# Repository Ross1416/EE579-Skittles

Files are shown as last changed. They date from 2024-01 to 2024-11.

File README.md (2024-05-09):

# EE579-Skittles

## RUSH (Robust Ultrasonic Skittle Hunter)

This repository is for RUSH (Robust Ultrasonic Skittle Hunter). RUSH (shown below) aims to autonomously play a game of skittles in a corridor without user input beyond the start. RUSH is based on a small, simple remote controlled (RC) car that was extensively modified to play the game with the aim of knocking over one or two black skittles while leaving any white skittles untouched. The winner of the game is determined by the quickest car to knock a black skittle over. However, if a white skittle is knocked over at any point in the round by the car, it is disqualified from the round. 

See TDF for more details.

<p align="center">
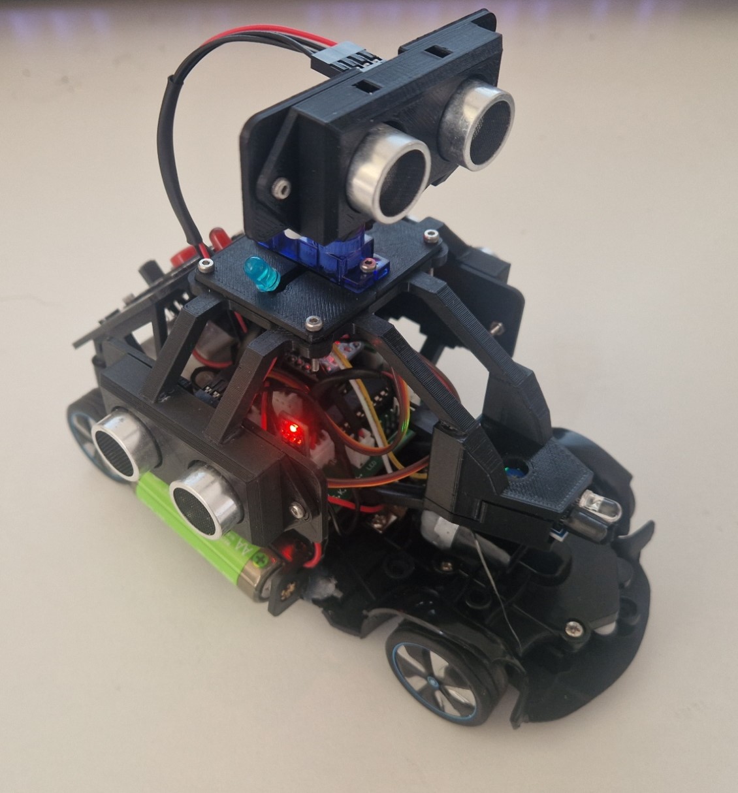
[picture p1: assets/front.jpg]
  
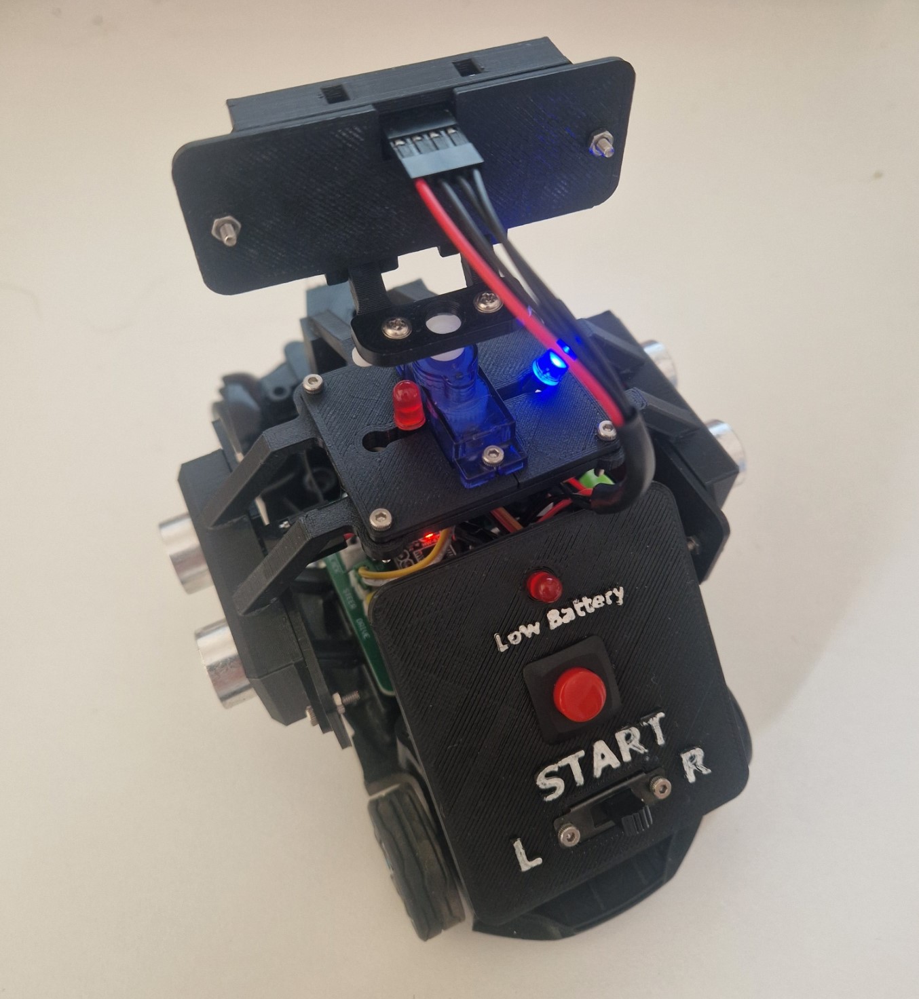
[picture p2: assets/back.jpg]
  
</p>

## Final Demo Day Results

### Heat 1

https://github.com/Ross1416/EE579-Skittles/assets/77679842/c86a0a25-7852-4bd4-9d39-e0872e5b2d3d

### Heat 2

https://github.com/Ross1416/EE579-Skittles/assets/77679842/7563ef13-5aec-49bf-9490-8388c58f7000

### Semi-final

https://github.com/Ross1416/EE579-Skittles/assets/77679842/7b09cfc3-21dd-4e16-b04d-08700aa69c5c

### (Anti-climactic) Final

https://github.com/Ross1416/EE579-Skittles/assets/77679842/db8d8a39-f27a-464d-a305-0642033d31cf

### 2nd Final (for fun)

https://github.com/Ross1416/EE579-Skittles/assets/77679842/e8e8383b-b6d6-447a-95fe-932a4549ee91

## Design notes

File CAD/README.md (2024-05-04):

See videos for disassembly instructions.

Top Sonar Removal

https://github.com/Ross1416/EE579-Skittles/assets/77679842/d813ab6a-119c-48e1-9a04-9669e5136af5

Servo Structure Removal

https://github.com/Ross1416/EE579-Skittles/assets/77679842/874d1653-7c2e-4df4-bafa-91eb13200755

Top Mount Removal

https://github.com/Ross1416/EE579-Skittles/assets/77679842/eb0d6709-a5ab-449e-a856-9e97e344e56b

Control Panel Removal

https://github.com/Ross1416/EE579-Skittles/assets/77679842/7449ef3e-6997-48b8-9b05-bda308c06ea9

Detailed ultrasonic disassbly 

https://github.com/Ross1416/EE579-Skittles/assets/77679842/6136482e-1819-41eb-bea9-b80b4085eafa

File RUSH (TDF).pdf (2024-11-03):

# Robust Ultrasonic Skittle Hunter

# (RUSH)

# Technical Documentation File

Samuel Kliskey | 202028443
Ross Inglis | 202032175
Andrew Law | 202009334
Signature: | Date: 08/05/24
Signature: | Date: 08/05/24

We hereby declare that this work has not been submitted for any other degree/course at this University

or any other institution and that, except where reference is made to the work of other authors, the

material presented is original and entirely the result of our own work at the University of Strathclyde

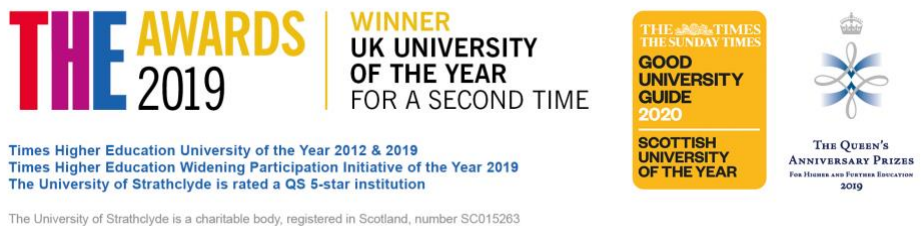
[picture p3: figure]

i

GitHub Repository: https://github.com/Ross1416/EE579-Skittles

## Contents

ii

## Nomenclature

BoM | Bill of Materials
GPIO | General Purpose Input / Output
IC | Integrate Circuit
IR | Infrared
LED | Light Emitting Diode
MSP | Mixed Signal Processor
NiMH | Nickel Metal Hydride
PCB | Printed Circuit Board
PLA | Polylactic Acid
RC | Remote Control
RUSH | Robust Ultrasonic Skittle Hunter
SONAR | Sound Navigation and Ranging
ToF | Time of Flight
uC | Microcontroller

iii

## List of Figures

Figure 12: MSP430G2553 IC (left) [2] , MSP430G2ET Development board (right) [3]

Figure 19: Low Battery Indicator Circuit on Control Board under motor driver (left)

Figure 25: Stages of wiring harness production: strip insulation (left), first stage crimp

Figure 41: Wiring harness (left), Programmer PCB connection (middle) and dev. board

Figure 44: Expected ultrasonic echo waveform at sensor (left) and on control board

iv

Figure 47: Servo test points on control panel | 38
Figure 48: Servo PWM control signal at maximum and minimum angle | 38
Figure 49: Skittle detection with Ultrasonic and Time of Flight (TOF) | 41

## List of Tables

Table 1: HC-SR04 Ultrasonic Sensor Specifications | 6
Table 2: Wiring Harness Connection Specifications | 16
Table 3: MSP430 Functionality and Purpose | 25
Table 4: Ultrasonic Testing expected resistances | 34

## 1 Introduction

This technical specification document details all information regarding RUSH (Robust Ultrasonic

Skittle Hunter) depicted in Figure 1. RUSH aims to autonomously play a game of skittles in a corridor

without user input (after setup) against an opposing car. RUSH is based on a small, simple remote

controlled (RC) car that was retrofitted to play the game and therefore RUSH will commonly be referred

to as the “car” in this document. The aim of the game is to navigate to and knock over one or two black

skittles whilst leaving any white skittles untouched. The winner of the game is determined by the

quickest car to knock a black skittle over. However, if a white skittle is knocked over at any point during

the two minute round by the car, it is disqualified from the round. The skittles were constructed of two

stacked and painted soup cans and are therefore often referred to as “cans” throughout.

This document covers all aspects of RUSH including a quick start user guide and hardware / software

descriptions. Also included is detailed guidance of how to perform troubleshooting and repair should

the car break or behave unexpectedly. This technical specification is intended for anyone with basic

technical knowledge that intends to use the car to play autonomous skittles, understand how it works,

aims to fix any issues that occur or make further improvements.

The base RC car (see Figure 2) that RUSH is based on was to be retrofitted with an array of sensors to

accomplish the goal while adhering to the guidelines stating no alterations to the chassis or drive train.

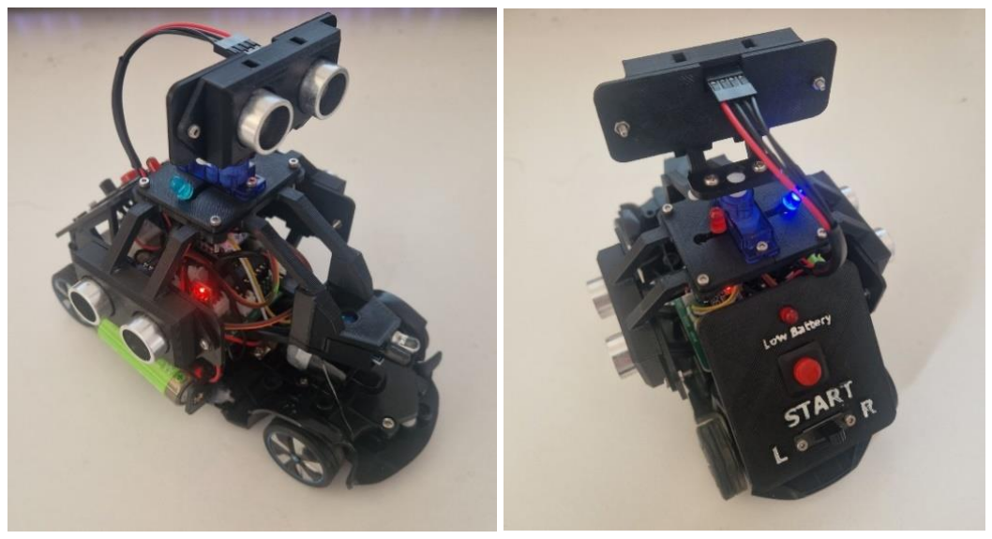
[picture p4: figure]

Figure 1: RUSH viewed from front (left) and rear (right)

Figure 2: Base RC car before modification [1]

## 2 User Guide

This user guide details instructions on how to quickly setup RUSH for a game of skittles. For the car to

function, the game must be setup in a long straight corridor. The corridor should be at least 10 m long

with an expected distance from the start line to the first skittle of at least 6 m. The walls of the corridor

should be unbroken and not have any alcoves or adjoining corridors in the game space as this will

disrupt the cars’ function. Some tolerance of wall geometry changing is accounted for in software but

it performs best where the wall is flat and performs worse if the wall has multiple changes close together

or passes an adjoining corridor. The setup of the car in the corridor should be roughly as seen in

Figure 3.

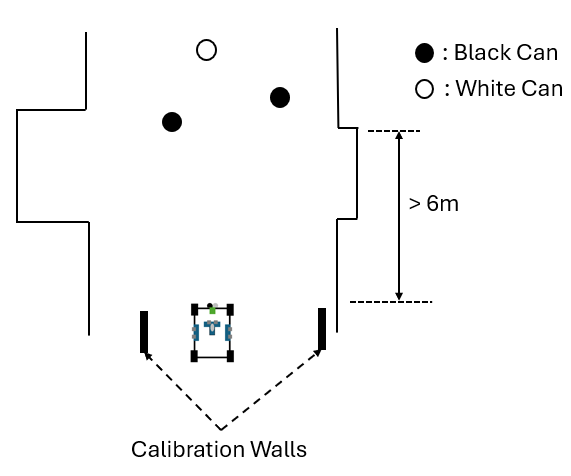
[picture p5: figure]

Figure 3: Setup Diagram

To begin the game, follow the steps below:

1. Place RUSH on start line: The car should be facing towards the game area with the skittles,

roughly in line with the black skittle that would be aimed for. In the example in Figure 4, it has

been aimed at the black skittle on the far right.

Figure 4: RUSH on start line

2. Setup calibration walls: The provided calibration walls should be setup either side of the car

in such a way that they are just beyond the skittle(s) that are aimed for. Construct the walls by

slotting the cardboard into the provided feet for stability. These walls are used in a calibration

reading to define the maximum distance at which the car will detect a skittle either side of the

car. Anything too far from the car at the side will not be detected as a skittle. These are also set

to limit the cars side view to not detect walls as skittle. Figure 5 shows the calibration walls

setup to ensure only the far-right black skittle is within limits and will therefore be targeted.

Figure 5: Calibration Walls setup to target black skittle on right

3. Turn on car: Using the switch on the underside (see Figure 6), turn on the car. One LED should

light with this indicating whether the left or right wall is currently selected for alignment.

Ensure at this stage that the top ultrasonic sensor is pointing forwards. If not, this will need to

be reattached pointing in the correct direction (as detailed in Section 3.2.1). If the low battery

indicator is illuminated at this point, the batteries should be removed and recharged before

continuing. Note that AA Alkaline batteries cannot be used as an alternative.

Figure 6: Power Switch

4. Select wall for alignment: Using the switch on the control panel, positioned between ‘L’ and

‘R’, select which wall the car will use to align to as it attempts to travel down the corridor

towards the skittles. The wall should be chosen depending on distance to car and how varying

and ‘flat’ it is. The car will tend to align better with a closer wall that does not vary much. The

wall chosen should also ideally not have the opposition car in between. In the example in Figure

7, the right wall is chosen for alignment as it is slightly more consistent that the left wall.

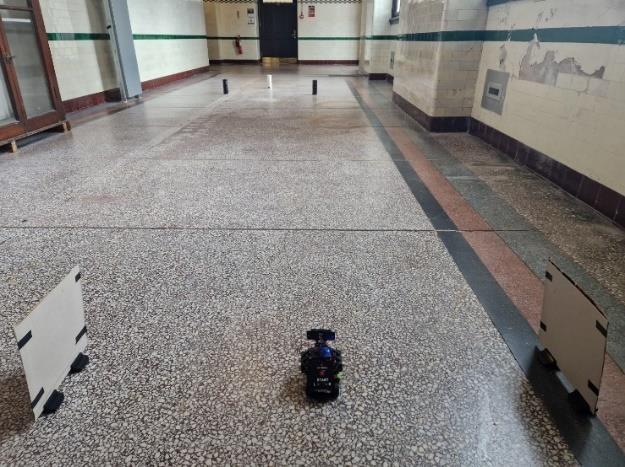
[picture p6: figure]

Figure 7: Right wall alignment chosen

5. Press Start button once: This stage performs the calibration with the walls placed previously.

After the button is pressed, both LEDs should illuminate (as seen in Figure 8), indicating the

car is ready to race. The calibration walls do not need to be removed.

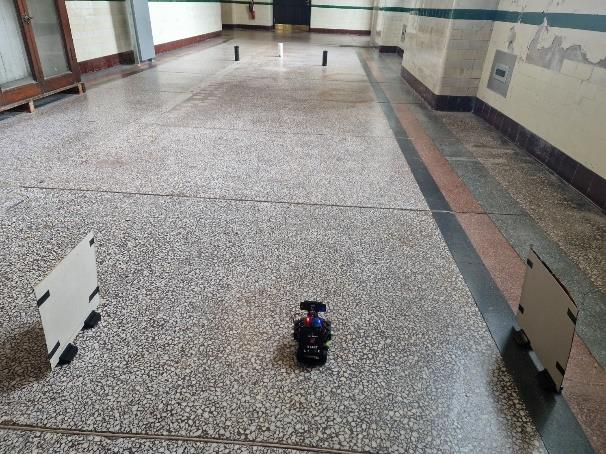
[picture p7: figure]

Figure 8: Car calibrated and ready to start

6. Race! When ready to race press the start button once more and watch the car begin the game.

Expected Operation: The car will travel forwards at a fast speed making small alignments to stay

straight in reference to the selected side wall. In this stage no skittles can be detected. When both red

and blue indicator LEDs illuminate, the car is in search mode and will slow down. It this mode it will

detect any skittles (provided it has been calibrated correctly). At this stage the car will stop upon

detecting a skittle and then slowly manoeuvre towards it. Once reaching it RUSH will determine its

colour, driving into it and knock it over if black or move around it if white.

## 3 Hardware Overview

The base RC car contained the mechanisms and motors for both steering and driving. For the car to be

able to manoeuvre down the corridor, detect the skittles, determine the colour, and knock it over if black,

it needed to be modified with an array of sensors and control systems.

For control of all functionalities of the car, an MSP430G2553 microcontroller is used in conjunction

with the bespoke PCB control board. All sensors and electrical systems externally connected to this

control board will be referred to as “peripherals” throughout this document.

To detect the cans and align with the wall, three ultrasonic distance sensors were used (two side facing,

one front) as seen in Figure 1. To determine the colour of the cans, a simple infrared sensor was used.

This section of the document contains detailed descriptions of how all the peripherals operates as well

as the structure and wiring used to connect them all together.

## 3.1 Electronic Peripherals

3.1.1 Ultrasonic Sensor (Distance)

The HC-SR04 ultrasonic distance sensor was chosen due to its low cost, ease of use and wide

availability. It emits ultrasonic waves and measures the time taken for the waves to bounce back from

the object, therefore distances can be measured all the while without interference from ambient light

like infrared (IR) based distance sensors. A pinout diagram of the HC-SR04 ultrasonic sensor is shown

below in Figure 9.

Figure 9: Diagram of HC-SR04 Ultrasonic sensor

The specifications of the sensor can be found in Table 1. Note that although the ultrasonic sensor is

rated to operate at 5 V, it was tested to consistently operate down to approximately 4.3 V.

Table 1: HC-SR04 Ultrasonic Sensor Specifications

Specification | Value
Operating Voltage | 5 V
Silent Current draw | 2 mA
Operating Current draw | 15 mA
Measurement Range | 2 cm to 4 m
Detection Scope | 30°

Due to the nature of ultrasonic sound waves and the sensor specifications, the detection scope of the

sensor is relatively large at up to 30° as depicted in Figure 10. This means that the sensor can detect

objects which are not directly ahead of it.

Figure 10: Ultrasonic Detection Scope

For the sensor to take a distance measurement, a short pulse of at least 10 µS must be applied to the

trigger pin. The sensor will then output a pulse from the echo pin for a time proportional to the time

taken for the emitted pulse to return. The distance (in metres) can therefore be calculated using Equation

(1) which also accounts sound waves travelling both to and from the object.

Distance (m) =

speed of sound × pulse time 2

(1)

Distance (m) =

343ms

−1 × pulse time
2

Since the ultrasonic sensor is powered at ~5 V but the MSP430G2553 microcontroller’s GPIO pins are

only 3.3 V tolerant, the echo pin output was stepped down using a voltage divider on the control board.

The output voltage of the voltage dividers with the set resistances for a 5 V input echo signal is

calculated in equation (2). This value of 3.4 V is within the microcontrollers GPIO voltage tolerance.

Vecℎo_out = 5 V ×

1 kΩ
1 kΩ + 470 Ω

= 3.4 V

(2)

3.1.2 Infrared Sensor (Colour)

With the car only needing to determine either black or white skittles, an Infrared (IR) sensor is used for

simplicity as a black skittle will reflect less IR light than a white skittle. The FC 51 IR sensor (see Figure

11) was chosen for its low cost and simplicity. It uses an LED to emit IR radiation alongside an IR

photodiode to detect any reflected IR radiation. The photodiodes receiver is wrapped with electrical

tape such that it is less prone to visible light and direct interference from the emitter. It provides skittle

colour detection from approximately 2 − 30 cm but for consistent results less than 11 cm.

Figure 11: Diagram of IR sensor

This sensor can be powered via 5 V or 3.3 V with the 5 V providing better range due to brighter

illumination of the IR emitter LED. However, the 5 V supply in RUSH is less consistent then 3.3 V,

therefore, 3.3V is used as the supply voltage to maintain distance calibration of the sensor. The output

of the sensor is digital with a “LOW” output indicating a great enough reflected light received and a

“HIGH” indicated for when too little reflected light was received. This is slightly counterintuitive as an

on-board LED uses the opposite logic to illuminate. The potentiometer on the sensor was used for

adjusting the sensitivity of the sensor.

3.1.3 Microcontroller

The MSP430G2553 microcontroller was selected for complete control of the operation of the car due

to its familiarity and low cost. This microcontroller operates at 3.3 V. Figure 12 shows the

MSP430G2553 IC and the associated development board that was used for programming the

microcontroller. Throughout the rest of this document this will often be referred to as “MSP430”.

Figure 12: MSP430G2553 IC (left) [2] , MSP430G2ET Development board (right) [3]

3.1.4 Motor Driver

The DRV8833 Dual H-Bridge Motor Driver module was used to allow the microcontroller to control

both steer and drive motors while drawing current from the battery (at nominal 4.8 V) and not the GPIO

pins (at 3.3 V). A diagram of the DRV8833 Dual H-Bridge Motor Driver module is shown in Figure 13.

Figure 13: Diagram DRV8833 Dual H-Bridge Motor Drive of [4]

3.1.5 Servo

For the car to function, it was required to be able to rotate an ultrasonic sensor to a known angle to find

skittles. To accomplish this an SG90 servo motor was chosen for low cost and wide availability. The

servo requires 5 V to operate. A diagram of the SG90 servo motor is shown in Figure 14.

Figure 14: SG90 servo motor [5]

3.1.6 Power Source

Four AA sized nickel-metal hydride (NiMH) batteries were used as the power source to allow

integration into the base RC car with minimal alterations. The NiMH batteries are rechargeable and

keep a very consistent nominal voltage of 4.8 V total (see Figure 16) which can power all systems rated

for 5 V. Note that no reverse polarity protection is installed, and so care should be taken when installing

the batteries. The fourth battery can be seen to be mounted on one side of the car which leads to RUSH

having a slight uneven weight distribution and pulls to the right whilst attempting to drive straight. This

was compensated for by adjusting the dial on the underside of the base RC car chassis to the left or “L”

side as seen in Figure 15.

Figure 15: Base RC car steering adjustment

The car cannot be powered off four AA Alkaline batteries as the starting voltage would be too high and

the inconsistent nature of the voltage levels would significantly alter the speed of the motors and

therefore the functionality of the car itself would be very inconsistent. It would be possible to power

the car off three AA alkaline batteries, however they would last a very short period before dropping

below minimum operating voltage of 4.2 – 4.3 V.

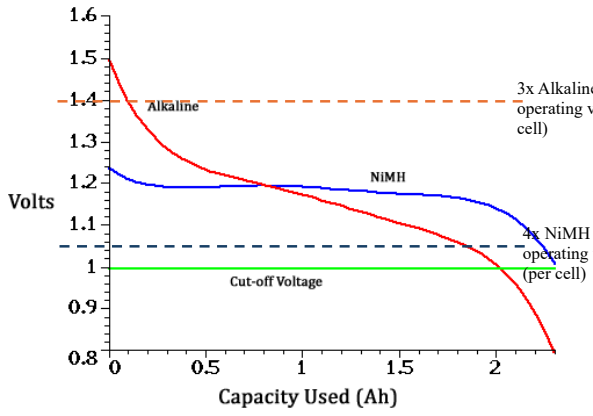
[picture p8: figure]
cell); (per cell)

Figure 16: Single cell Alkaline vs NiMH Voltage discharge graph [6]

When fully charged, the battery was measured to have a starting voltage of 5.329 V which quickly

dropped to the nominal 4.8 V.

To obtain the steady 3.3 V required for the microcontroller and IR sensor, a low-dropout DC linear

voltage regulator was used, specifically a through-hole module containing the AMS1117 and all

required passive components seen in Figure 17. A through-hole module was used to allow quick and

easy replacement should if break.

3x Alkaline Minimum
operating voltage (per

4x NiMH Minimum
operating voltage

Figure 17: AMS1117 3.3 V Regulator Module

3.1.7 Control Board

All systems are connected and managed through the control board seen in Figure 18. Highlighted in the

diagram are the colours of the wires to be connected to the Dupont headers to ensure correct orientation

of connection for the servo and programming header. The remaining connectors cannot be orientated

incorrectly due to the header design. The labelled test points on the rear of the board can also be seen

in the figure with label “Tr-T” being corrected as PCB label was placed at incorrect position. Note the

dotted green circles as these highlight indicators for the orientation of the MSP430, motor driver and

3.3 V regulator. For full schematic of Control Board, see Appendix 11.1.

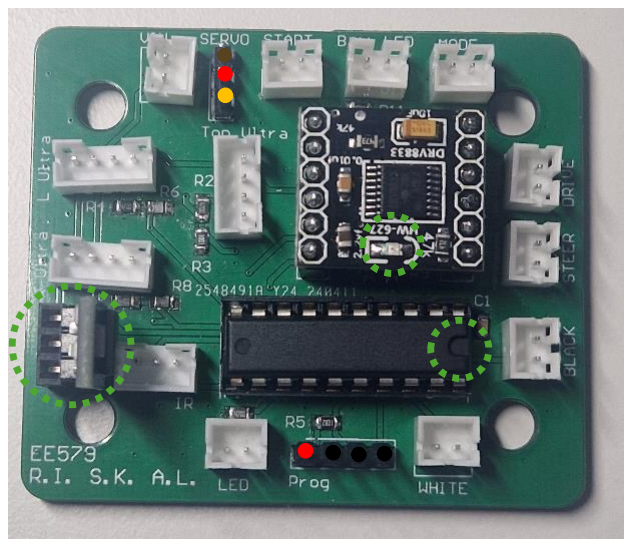
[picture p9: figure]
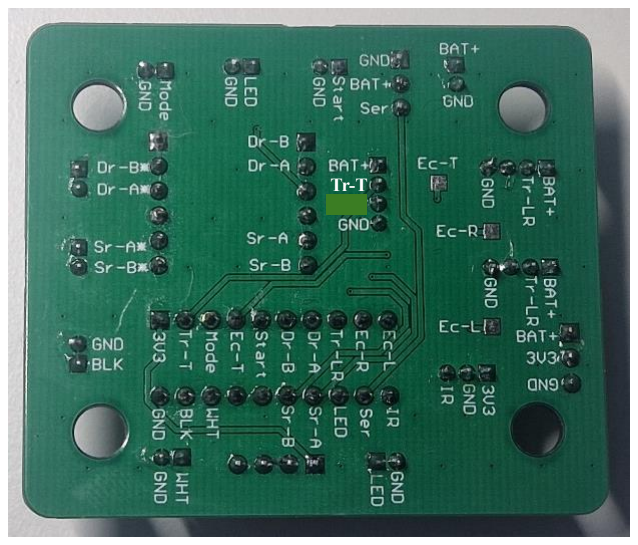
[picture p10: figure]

Figure 18: Control Board PCB top (left) and test points (rear).

3.1.8 Low Battery Indicator

Contained on the control board is a low battery indicator circuit seen in Figure 19. It uses a Zener diode

in reverse bias as a set voltage reference for comparison to the current battery voltage. The

potentiometer shown is used to vary the proportion of the battery is compared against the set Zener

voltage and therefore controls the battery voltage at which the low battery indicator illuminates. It is by

default set to illuminate at approximately 4.3 V as this was the lowest measured voltage that the whole

car would consistently correctly operate at.

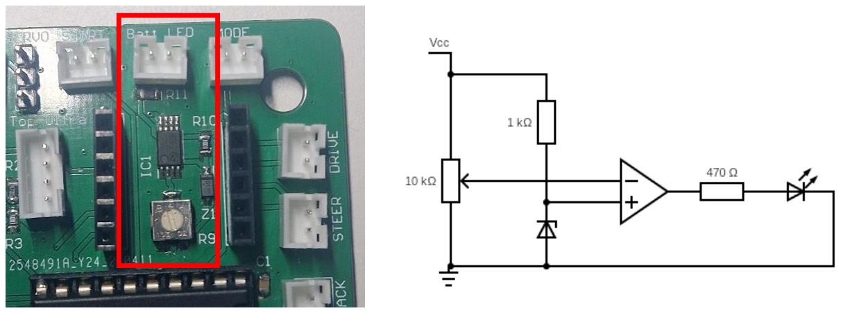
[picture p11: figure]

Figure 19: Low Battery Indicator Circuit on Control Board under motor driver (left) and circuit diagram (right)

## 3.2 Structure and Mounting

To house all the required electronics a mounting structure was designed to replace the base RC car’s

cover. This section of the report details the methods of (dis)assembly of the structure and wiring harness

construction. All bolts used in the structure are various length M2 bolts with a 1.5 mm Allen key bolt

head except for the screw used to mount the top ultrasonic structure to the servo which uses a Phillips

head.

All electronic peripherals and structure components are recorded in the Bill of Materials (BoM) listed

in Appendix 11.2.

3.2.1 Disassembly Instructions

To fully disassemble the car (as necessary for testing and upgrades), there are four main stages listed in

order of disassembly as: Top SONAR Ultrasonic structure, Top SONAR servo structure, Upper Main

Structure and additionally the Control Panel structure which can be removed at any stage as it is not

directly connected to the other structures. Each structure consists of multiple 3D printed parts that are

glued and/or bolted together. The structures are used to mount the sensors and other electrical

peripherals.

The exploded view diagram of the disassembly of the Top SONAR Ultrasonic structure can be seen in

Figure 20 with the BoM listing of each of the disassembled parts. This stage of disassembly requires

the removal of the single Servo Screw with a Phillips head and also two M2 nuts and bolts if removal

of the ultrasonic sensor is required. When the car is first turned on, if the Top SONAR ultrasonic sensor

is not pointing forwards, the full structure should be taken off by removal of the servo screw (M-19)

only, realigned and then reattached by replacing the screw.

Figure 20: Top SONAR Ultrasonic structure Disassembly Diagram

Figure 21 shows the next stage: Top SONAR servo structure disassembly. This stage could occur after

the Top SONAR Ultrasonic disassembly. It requires the removal of six M2 nuts and bolts along with

four washers.

Figure 21: Top SONAR servo structure Disassembly Diagram

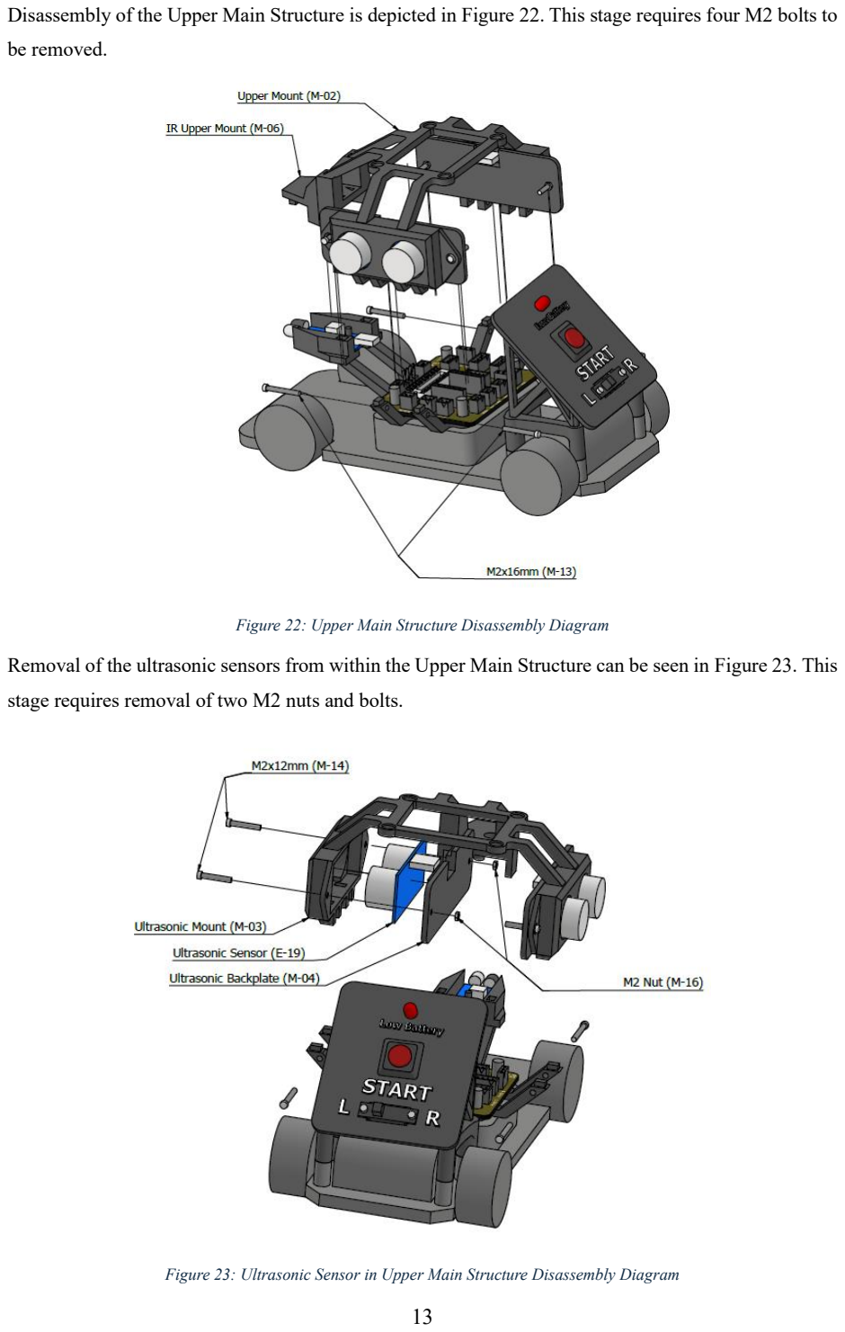
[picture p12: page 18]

Disassembly of the Upper Main Structure is depicted in Figure 22. This stage requires four M2 bolts to

be removed.

Figure 22: Upper Main Structure Disassembly Diagram

Removal of the ultrasonic sensors from within the Upper Main Structure can be seen in Figure 23. This

stage requires removal of two M2 nuts and bolts.

Figure 23: Ultrasonic Sensor in Upper Main Structure Disassembly Diagram

The full disassembly diagram of the Control Panel structure is seen in Figure 24. To remove the control

panel structure from the chassis, only two M2 bolts need to be removed and the panel lifted up as one.

The LED within the panel is friction mounted and can be removed from pulling from the reverse side

of the panel. The Start button can be removed by pushing from the underside of the panel, ensuring it

is disconnected from the Control Board. The slide switch requires two M2 nuts and bolts to be removed.

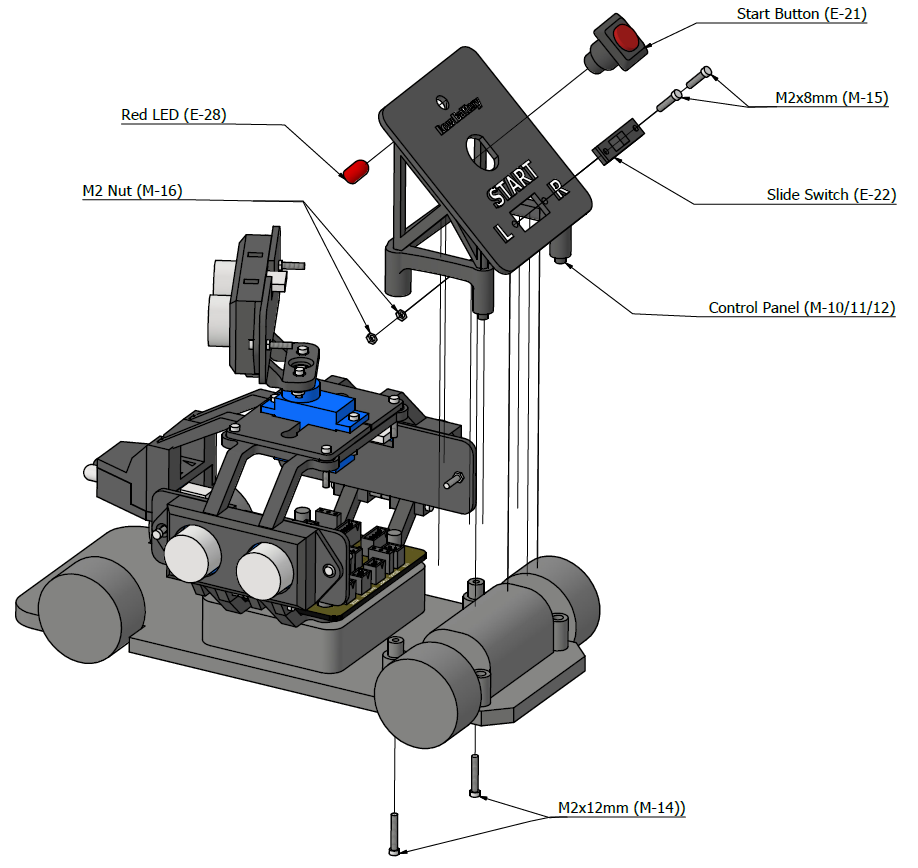
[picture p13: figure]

Figure 24: Control Panel structure Disassembly Diagram

All sections of the mount are 3D printed with PLA (polylactic acid) material. The BoM in Appendix

11.2 lists each individual part, which were glued and bolted together to make combined structures. All

files required for printing are found in the projects GitHub repository.

3.2.2 Wiring Harness Assembly

To electrically connect the components to the circuitry of the control board, wiring harnesses are used.

All harnesses were tested to stay firmly connected after three consecutive drop tests from 20 cm onto a

hard surface. This section describes the methods for producing them in case of breakages. To determine

if a wiring harness requires replacement, refer to Section 6.

The harnesses are made using two colours of wires: red and black. In every connection, the red wire

defines the VCC connection to ensure correct orientation of the Dupont connectors. On the PCB side,

most of the connections use JST-PH2.0 which cannot be inserted in the wrong orientation. However, all

sensors use Dupont 2.54mm pitch headers which could be connected in the wrong orientation if care is

not taken.

Connections to both motors and the battery are 2-pin JST-PH2.0 and were a part of the base RC car and

so are not covered in this section however the same procedures would apply. The servo also contains

its own connection and therefore if it were to break, a whole new servo would be required.

The LEDs, buttons and switches use 2-pin JST-PH2.0 connectors on the control board side and on the

component side they are directly soldered to the pins with heat shrink tubing encasing the connections

to insulate them. Note that the blue indicator LED (connected to BLACK header on the control board)

requires a 470 Ω resistor to be soldered in line.

To produce the wiring harnesses the following steps should be followed:

1. Cut all wires to length listed in Table 2.
2. Strip both ends of each wire
3. Crimp each end with either a JST or Dupont crimp (see Figure 25) depending on listing in Table

2 or solder connection if listed. For further guidance on crimping, refer to [7].

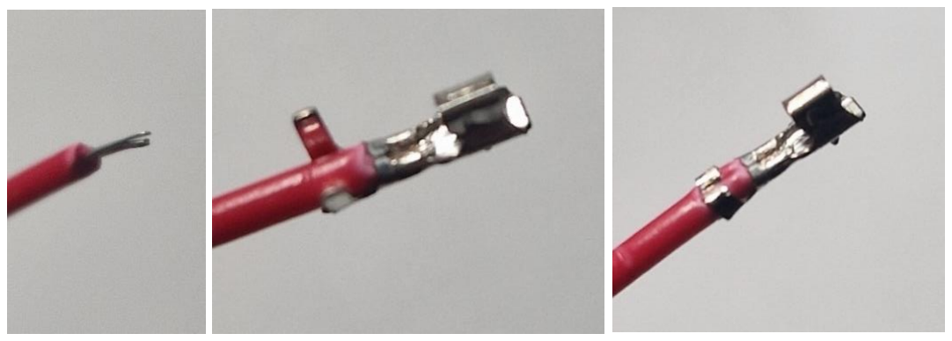
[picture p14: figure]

Figure 25: Stages of wiring harness production: strip insulation (left), first stage crimp (middle) and last stage crimp (right)

4. Insert crimped wire ends into connector specified in Table 2. For the order of the wires in the

connector refer to the pinout of the peripheral and match with the label on the reverse of the

Control Board. At this stage the full bundle of wires can be heat shrinked or taped together.

Table 2: Wiring Harness Connection Specifications

Connection (PCB Label) | Number of Wires | Length (cm) | PCB Connector | Component Connector
Right Ultrasonic (R Ultra) | 4 | 7 | 4-pin JST-PH2.0 | 4-pin Dupont
Left Ultrasonic (L Ultra) | 4 | 8 | 4-pin JST-PH2.0 | 4-pin Dupont
Top Ultrasonic (Top Ultra) | 4 | 14 | 4-pin JST-PH2.0 | 4-pin Dupont
IR Sensor (IR) | 3 | 6 | 3-pin JST-PH2.0 | 3-pin Dupont
Start Button (START) | 2 | 5 | 2-pin JST-PH2.0 | Soldered
Red Indicator LED (LED) | 2 | 6 | 2-pin JST-PH2.0 | Soldered
Blue Indicator LED (BLACK) | 2 | 6 | 2-pin JST-PH2.0 | Soldered with inline 470 Ω resistor
Side Select Switch (MODE) | 2 | 5 | 2-pin JST-PH2.0 | Soldered
Low Battery LED (Batt LED) | 2 | 4 | 2-pin JST-PH2.0 | Soldered

## 4 Software Overview

Detailed in this section is the functionality of RUSH and the software design used to achieve it. The

software is organised as a state machine with a scheduler used to control the transitions between states.

Some sub-sections of the software overview require some basic knowledge of programming and how a

scheduler operates. All code is written in C and can be found on the project’s GitHub repository (EE579-

Skittles/CarReorganised/).

## 4.1 General Functionality

The program software operates using states that control the cars behaviour based off its current state.

Figure 26Error! Reference source not found. depicts the states and transitions between states

implemented. The use of states aids modularity as if extra functionality is to be added, it is easy to insert

a new state. Having separate states also aids in debugging and improvements as issues can be narrowed

down to a particular state. A set of MACROs at the start of main.c define all the states used.

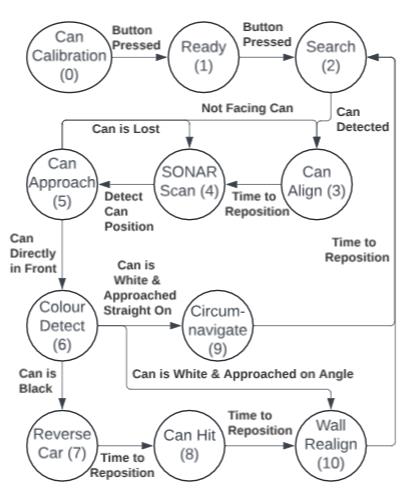
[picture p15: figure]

Figure 26: Functional State Diagram

The initial state on power up, Can Calibration, does nothing until the start button is pressed. When the

button is pressed the ultrasonic sensors on each side of the car take an average of several readings. The

average is used to determine the furthest distances either side at which cans will be detected as such.

Any distances readings beyond this calibration can be attributed to the wall at the boundary of the play area. One second after the first button press, the Ready state is then entered. This state waits for a further

start button press before starting the autonomous phase of the car.

In the Search state the car drives forward whilst constantly aligning straight to the wall ensuring that

the car does not veer off course. This alignment performs best when there are no changes in the wall

geometry. When an ultrasonic sensor detects a can closer than the set threshold, Can Align state is

entered to confirm the can reading and realign the car to be able to approach the can. SONAR Scan is

then used to sweep through the range of the servo which has an ultrasonic sensor attached. The

ultrasonic sensor combined with the servo determines where the can is relative to the car. After finding

the can, the state Can Approach is entered. During this state the top ultrasonic sensor, referred to as

SONAR, alters to always point at the can and the car drives on the heading of the SONAR to the can.

If the SONAR has lost sight of the can, then the car returns to SONAR Scan state to refocus on to it.

Having reached the can, the angle of the SONAR to the can is checked. If the angle is too large in either

direction from straight ahead then the main car body, where the IR sensor is mounted, is not considered

straight enough to the can. The car then reverses to readjust and reapproach. This is required for the

mounted IR sensor to determine whether the can is black or white which needs to be close to the can

and facing the can directly to function correctly. It also aligns the car correctly should a black can be

detected and therefore should be knocked over. When the can has been approached at a good enough

angle the state is changed to Colour Detect. In this state the IR sensor is read to determine the colour of

the can.

If the colour is black, then the car enters Reverse Car followed by Can Hit to knock over the can. If the

colour is white, then the car enters one of two states. If the can was originally detected in front of the

car, then the car enters Circumnavigate which drives the car around the white can to get past it. If the

can was originally detected by a side ultrasonic sensor and approached, then the Wall Realign state is

used to get the car back away from the can and start to straighten the car parallel with the wall. The Wall

Realign state is also used after a black can has been hit. After realigning to the wall, the Search state is

re-entered to start searching for more cans.

## 4.2 Individual State Complete Functionality

4.2.1 Can Calibration

The first car state is Can Calibration. In this state the car does nothing until a user presses the button.

At this time, each side ultrasonics takes five readings to determine an average distance. The user should

setup the calibration walls as in Section 2 to calibrate the furthest distance that a can will be detected

at. This is illustrated by Figure 27 This distance would ideally be slightly closer than the closest wall of

the full length of corridor play area. If a single can is to be aimed for, the calibration walls can be setup

to do so by bringing them closer to the car such that they are only just either side of the can being aimed

for.

The car will slightly drift left or right during operation even with the align to wall functionality. Because

of this nature it is better to use the provided makeshift calibration walls to set a distance between the

can and the closest wall to allow for greater tolerance as the car ends up closer to or further from the

wall whilst also being able to detect cans that appear closer than the makeshift calibration wall. This

average is used throughout the program to determine if a can has been detected by reading a distance

closer than the threshold set.

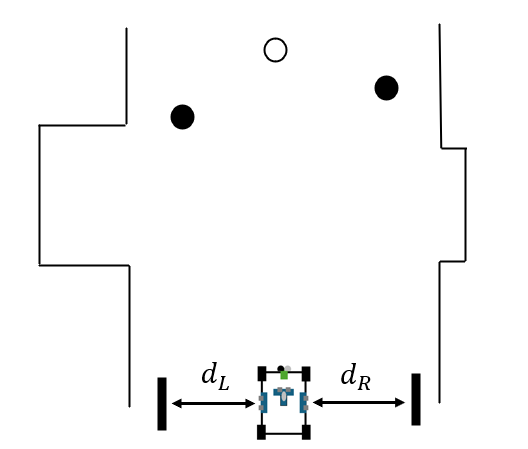
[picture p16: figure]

Figure 27: Can Calibration State Illustration

In this state the side select switch can be used to set the left or right ultrasonic to control the wall side

that is aligned to. This was implemented to account for starting on either the left or right of the

opposition car in the space. The left (red) or right (blue) LED’s are lit when the switch is pressed. The

state will change to Ready one second after the initial button press.

4.2.2 Ready

Upon changing to the Ready state both indicator LEDs are lit to indicate readiness for the user input

and to start autonomy. The Ready state awaits the user pressing the button. When the button has been

pressed and debounced successfully the car enters the Search state. This state on the button press also

schedules the enabling of search flag which is discussed in Section 4.2.3.

4.2.3 Search

The purpose of the Search state is to drive through the space using the three ultrasonic sensors to detect

the position of cans. A can is detected when the SONAR ultrasonic, which is pointed forwards, detects

a can in front; or when one of the side ultrasonics reads a distance shorter than the Can Calibration

initial readings. When a can is detected, the source of direction (Straight, Right, Left) is noted for future

use. The cans on the side are only detected when the search flag is enabled. The reason to have a search

flag is that no cans are expected to be seen for the first 6 metres (as per the game rules) so disabling

searching for an amount of time before then allows for the car to get to the region the cans are expected

to be faster. It can be faster whilst not searching as the ultrasonic sensors are read in a round robin and

at high speeds a can could be missed. The ultrasonics are triggered in a round robin to mitigate

interference. After the left is read the right is triggered, when right is read top SONAR is triggered and

then back to the left.

Simultaneously to the can detection, the alignToWall() function ensures that the car is driving straight.

The function is called when the relevant ultrasonic to the wall being aligned to is read. The relevant

ultrasonics readings are analysed to determine the trend in the data and corrects the car heading with a

short 50 ms turn to re-adjust the car. Figure 28 depicts the decision-making process of the wall

alignment.

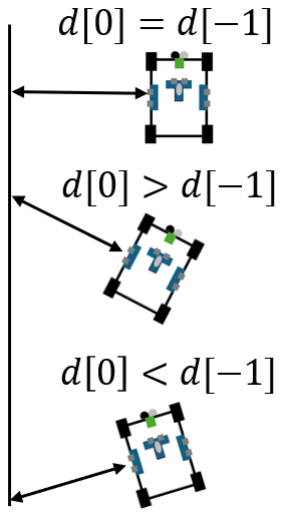
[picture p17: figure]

Figure 28: Align to Wall Decision Making

If the readings are trending closer, then the car is travelling toward the wall, so the car needs to readjust

by turning away from the wall. The opposite is true as readings increase. When, withing tolerance, the

distance is the same as previous readings then continue driving straight.

4.2.4 Can Align

To account for a false reading or detection of the other car a two second delay is implemented before

rechecking that the can is still detected where it is thought to be. The car, in the case of a left or right

can detection, may have driven past the can by the time it comes to a complete stop and so a reverse is

also implemented to make car become parallel to the can. When a left or right can is verified to be there,

the car reverses in the opposite direction. This is so that the car should then be roughly facing the can.

At this point the state is changed to SONAR SCAN. In the case of a front detection the car immediately

enters SONAR SCAN upon confirmation of can presence. If a can is not confirmed, then the car re-enters

the Search state. Figure 29 depicts the car behaviour on entering this state, confirming can location and

realigning to face can.

Figure 29: Left Can Confirmation & Alignment

4.2.5 SONAR Scan

The SONAR Scan purpose is to find the cans position in the space at a relative angle to the car and the

distance it is away. The Servo is initially turned clockwise and then takes five readings at each angle

moving anti-clockwise. The average reading at each angle is stored. By default, the scan takes the

averaged readings at fifteen angles of the full sweep. Upon completion of the sweep the distance

readings are analysed. An ‘anomaly’ is detected when the distance at the checked angle is significantly

shorter than the previous angle distance. The anomaly is registered at every angle whilst the shorter

distance is read. This process is depicted in Figure 30.

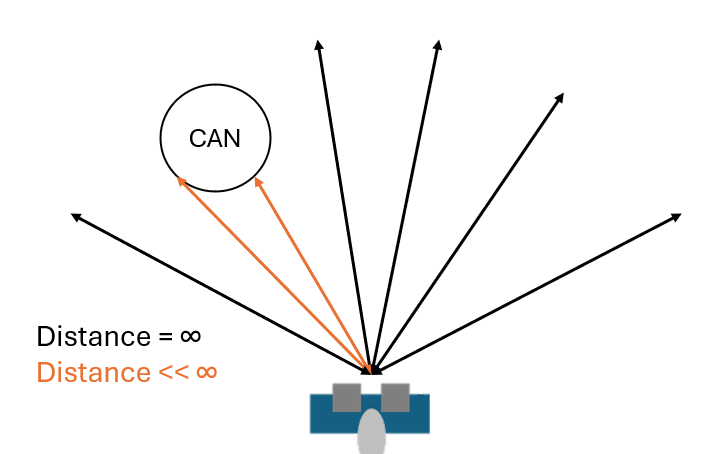
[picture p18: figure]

Figure 30: SONAR Anomaly Detection

The SONAR can detect multiple anomalies in a sweep and can also differentiate between two anomalies

if one can is in front of another. During the sweep if an anomaly is detected the red LED will light and

if a second anomaly is detected in front of a current anomaly, then the blue LED will also light. To find

the closest anomaly all the distance readings on each angle are averaged and the closest anomaly is

chosen to be locked on to. Where an anomaly is present for multiple angles the SONAR will lock on to

the median angle of where the anomaly is present. If no anomaly is found Search mode is returned to

but practically this never occurs as walls also cause anomaly readings. Once the anomaly is locked on

to the Can Approach state is entered.

4.2.6 Can Approach

In the Can Approach state the car drives to the heading of the SONAR. For example, if the servo is

pointing left of the centre position (pointing straight) the car drives to the left. Whilst the car is moving

the SONAR stays in position. As the car is changing angle the SONAR will lose sight of the can. At

this point the car will stop, and the SONAR will attempt to re-find the can in a short number of angle

rotations in the expected direction of the can. The direction the can should be is predictable relative to

the car when it has been lost. If the car was turning left and the SONAR is no longer looking at can then

the can will likely be to its right, this reasoning is depicted by Figure 31.

Figure 31: Can Approach with Locking on to Can

The SONAR does a couple of checks on angles in the expected direction of the can when can is out of

view. If the can is not found within checking four angles, then the SONAR SCAN state will be re-entered

to get a lock on the can again.

When the car reaches within IR reading distance of the can the angle of the SONAR is checked to ensure

that the car is facing the can head on. If the angle is not straight enough the car will reverse and turn to

get a better angle before using SONAR SCAN to lock on to the can and approach again.

When the angle and distance to the can is appropriate the Colour Detect state is entered.

4.2.7 Colour Detect

In Colour Detect the IR sensor is read to determine if the can is black or white. If black is detected, then

Reverse Car is entered. If white is detected, then either Wall Realign is entered or Circumnavigate. Wall

Realign is entered to get the car back parallel to the wall if the can was found on the left or right and

therefore approached at an angle. Circumnavigate is entered if the can was detected straight on and

therefore approached from the front.

4.2.8 Reverse Car

The car is reversed for a second before entering Can Hit. This allows the car space for acceleration so

that the car can hit the can with enough force to knock it over.

4.2.9 Can Hit

In Can Hit the car drives forward at full speed to knock the can over and then enters Wall Realign.

4.2.10 Wall Realign

In the Wall Realign state the car reverses straight and then reverses in the direction which makes it

become parallel with the wall. The direction to realign is known from the cans original detect position.

This is a rough estimate to get parallel which is followed up by the align to wall functionality until the

car determines that it is straight with the wall as it has not had to readjust for multiple readings. When

straight the car re-enters search mode to continue searching for cans. In this time of realignment, no

cans will be detected.

4.2.11 Circumnavigate

The Circumnavigate state performs several movements to manoeuvre around the white can that has

been approached and detected straight on. However, the first step is to check which wall is further away.

This allows the car to navigate around the side of the can with more space if the can is close to the wall.

The order of steps taken by the car is depicted in Figure 32 before re-entering the Search state to

continue searching for cans.

Figure 32: Circumnavigate Movements

## 4.3 Scheduler and Event Flags

To aid the state structure used, a scheduler and set of flags are employed. These are implemented as

their own type structures to group all these types of variables together.

The scheduler is kept on time by Timer A0 which is used to trigger an interrupt every 2 milliseconds

and add this to the running track of time. The running track of time counts to 5 minutes before resetting

to zero. A structure for time type variables was created that contains integer second and integer

millisecond variables. To set a time for an event to occur the timeIncrement() function is called with

arguments of the event that should occur and when it should occur. The function accepts a pointer to a

time variable and an integer value for a second and a millisecond respectively. It will then set the input

time variable to the current time plus the input second and millisecond values. Each time the Timer A0

interrupt occurs, a flag is set high to check all the schedule variables and determine whether it is time

to act on an event or not. Upon the time of the event, depending on the nature of the event either a sensor

is triggered; a flag is set high to be dealt with elsewhere; a parameter is changed; or an action is

immediately dealt with.

The event flags occur when certain conditions are met. This includes the debouncing of buttons; the

completion of ultrasonic readings; the changing of DC motor behaviour and the changing of states.

Each flag is attended and alters car behaviour or sets other flags to be attended within the control of

each state.

The scheduler and flags assist with peripheral control as well as general timings of delays for code

functionality. For example, the Circumnavigate state has the car drive in each heading for set durations

which is controlled by the scheduler. Within the main code, states can be entered by setting the nextState

variable to the desired state to transition to and setting either the flags.stateChange high or setting a

time with timeIncrement(&Schedule.stateChange, sec, ms) for the state to change at.

## 4.4 Microcontroller Utilisation

Multiple internal MSP430 functionality was used for internal timing operations as well as peripheral

control. Table 3 contains a list of the MSP430 functionality used and its purpose. For how further details

on the MSP430G2553 components used, refer to its datasheet [8].

Table 3: MSP430 Functionality and Purpose

Component Used | Purpose
Timer A0 (Counts to 2 ms) • ISR 0 • ISR 1 | Scheduler Clock & SONAR Reading • Increment and flag scheduler timer. • Capture SONAR Ultrasonic Pulse (P1.2)
Timer A1 (Counts to 20 ms) • Outmode 7 with TA1CCR2 • ISR 1 | Sonar Servo Timings & Side Ultrasonics • Servo PWM signal (P2.4) • Capture Side Ultrasonic Pulses (P2.1 & P2.2)
Port 1 • P1.0 • P1.1 / Pull-Up • P1.2 • P1.3 / Port Interrupt / Pull-Up • P1.4 • P1.5 • P1.6 • P1.7 | • SONAR Ultrasonic Trigger (Output) • Side Switch (Input) • SONAR Ultrasonic Echo (TA0 Capture ISR 1) • User Button (Input with Interrupt) • Steer Motor Left (Output) • Steer Motor Right (Output) • Drive Motor Forward (Output) • Drive Motor Back (Output)
Port 2 • P2.0 • P2.1 • P2.2 • P2.3 • P2.4 • P2.5 • P2.6 • P2.7 | • Side Ultrasonics’ Trigger (Output) • Right Ultrasonic Echo (TA1 Capture ISR 1) • Left Ultrasonic Echo (TA1 Capture ISR 1) • Infrared Sensor (Input) • Servo PWM control (TA1 Output) • Red LED (Output) • Blue LED (Output) • Unused in code

## 4.5 Peripheral Control

Each peripheral type has an associated header and c file to define an associated component type

structure variable that holds certain values the component will require. The files also contain any

associated functions to setup and control the peripheral. This makes the code modular and easy to use

so that the component variable with its relevant information can be instantiated in the main file and only

the pointer of the component variable is passed to external functions to setup, read and control the

peripherals. All peripheral types and how they are controlled are covered in this section.

4.5.1 Ultrasonic

The HC-SR04 uses two pins to start and return readings. The ultrasonic variable type contains the port

with the trigger and echo pins used as well as the time at which the returned pulse changes and therefore

the length of the returned pulse. The setup of the ultrasonic uses a function that accepts the pointer to

the ultrasonic data. This function uses the pins input to setup the pins and the relevant timer capture

compare functions to determine whenever the pulse polarity changes. Integral to the ultrasonic setup is

that each timer is setup in the main code for the capture compare interrupts to capture the time values

when the edges are detected.

The HC-SR04 is triggered using a 20 micro-second pulse from the setup trigger pins. When the

ultrasonic is triggered the timer capture compare interrupt is reconfigured to be activated by the echo

pin of the desired ultrasonic. The interrupt, contained in the main file, occurs when the pulse changes

polarity. When both the up edge and down edge have triggered the interrupt the difference in time

between the two edges is calculated. This functionality is visualised in Figure 33. The length of pulse

is relative to the distance that the ultrasonic sensor has measured. In the main file when a new distance

reading has been returned a flag is set high that indicates for the rest of the code that the new distance

reading is ready to be utilised.

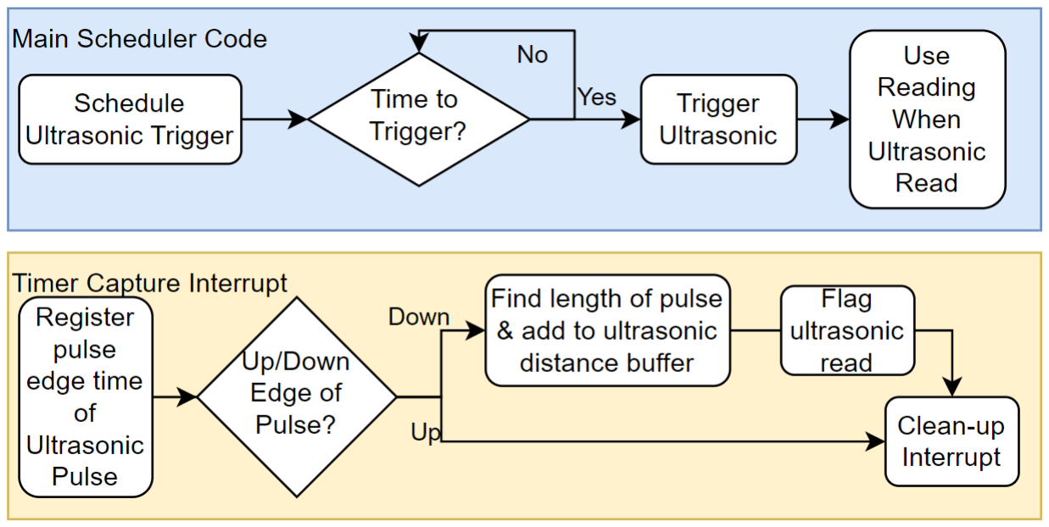
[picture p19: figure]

Figure 33: Ultrasonic Reading Control

4.5.2 Infrared

The infrared (IR) sensor variable structure contains the port and pin it is connected to as well as the

colour that has been read. To setup, the pin is set to be an input. A function, “IRRead()” is used which

sets the current feedback from the IR sensor to the colour variable where a white skittle is found when

the value is low and black skittle found when the value is high. The “IRRead()” functionality is shown

in Figure 34.

Figure 34: IR Control

4.5.3 User Interface

The user interface consists of a button, a switch and two indicator LEDs. The LEDs are setup with the

port and pin it is connected to. The switch and button classes are the same as the LED with the additional

variable of val which is the value populated when the component is read to be high or low. To setup the

switch and buttons, the selected pin is set to have an internal pull-up resistor. Meaning that when the

switch or button is used to pull the input to ground, the voltage is changed from high to low. The

switches nature is to be steady high or low whereas the button is pressed and released. To confirm the

button has been pressed an interrupt has been enabled to flag the event occurred. Also, due to the

mechanical “bouncing" of the button, when pressed and the interrupt triggered, a time of 20

milliseconds in the future is set to check the button again for debouncing and ensure the button was

intentionally used. There are functions to setup each of the user interface components; read the buttons

and switches; as well as control the LED outputs.

4.5.4 Servo Motor

The servo motor is setup with the variables ‘direction of rotation’, ‘angular displacement of a rotation’

and the ‘PWM pin’ it is connected to. To setup the servo, Timer A1 is used to create a PWM (Pulse

Width Modulation) signal that defines the angle the servo should rotate to. This involves setting the

maximum value of the timer and the value at which the connected timer output should switch from high

to low. The period of the PWM signal used is 20 milliseconds and an appropriate TA1CCR0 value is

selected of 20,000 when the SMCK of 1 MHz is used. This is depicted in Figure 35. The output can be

connected to pins 2.4 or 2.5 [8]. For this project 2.4 was selected.

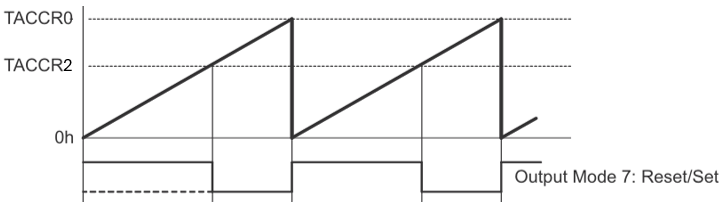
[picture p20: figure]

Figure 35: Output of Timer Linked Pin in Mode 7 [9]

To rotate the servo a function is used to add or subtract the time that the PWM period should be high

for (the duty cycle) using the direction and the angular displacement values instantiated. The ideal servo

range of motion is from 0 to 180 degrees using pulse widths from 1 to 2 milliseconds. These timings,

with SMCK, relate to TA1CCR2 values of 1000 to 2000. Through testing it was found that the full 180

degrees cannot be rotated and that the maximum range that is achieved occurs between TA1CCR2

values of 700 to 2300. The servo can be turned in code using the function servoTurn() which accepts

the pointer to the servo information and will turn in the direction and amount specified in the variable.

4.5.5 DC Motor Control

A DC motor is setup with the pins it is connected to, the direction the motors should spin and a variable

of PWM type. The PWM type is defined to allow the DC motor to be controlled at differing speeds.

The PWM structure contains the total PWM period, the duty cycle time and whether the PWM signal

is currently high or low. In the main file, the PWM times are used to regularly schedule the times that

the PWM state changes at. The functionality provided allows setup of the pins to control the DC motors

and the function motorOutput() sets the relevant pins high or low based on the direction the motor is set

to move. The PWM signal to control the motor speeds is generated using the scheduler rather than using

a dedicated timer as all timer functionality is already used for other functions.

## 5 Tuning Parameters for Performance

This section details some of the tuneable parameters that can be altered within the main code as seen in

Code | Extract | 1 | with | some | commonly | adjusted | parameters | highlighted.

“TIME_BEFORE_SEARCHING” should be tuned in association with “SPRINT_SPEED” as both will

alter the distance before entering search mode and skittles can be detected. Increasing

“SPRINT_SPEED” too much could cause the car to lose wall alignment while increasing

“FIND_SPEED” too much could cause skittles to be undetected. “MAX_FRONT_DETECT” defines

the distance where a skittle will be detected in front. Increasing this too much could cause irregularities

in the ground (such as large cracks) to be picked up as skittles.

Code Extract 1: Changeable Parameters in main code

//============================================================================== // CHANGEABLE SETTINGS MACROs //------------------------------------------------------------------------------//Scheduler control
#define TIMER_INC_MS | 2 | //Scheduler interrupts period (2 ms)

//Drive Speeds
#define MOTOR_PWM_PERIOD | 100 | //PWM period of motors.

//Wall readings control
#define WALL_READINGS | 5 | //Number of wall readings remembered

(MAKE 1+2^x)
#define AVERAGE_SHIFT | 2 | //log2(WALL_READINGS-1), used for

computationally efficient find average
#define | TIME_BEFORE_SEARCHING | 6 | //Time in seconds on start before

searching
#define | FIND_SPEED | 35 | //Speed once in search time

#define | SPRINT_SPEED | 60 | //Sprint speed to get to search area

//SONAR Reading control
#define SONAR_READINGS | 5 | //Make equal to wall readings

#define | MAX_FRONT_DETECT | 2500 | //Distance front can is detected in

#define ANOMALY_DISTANCE 500 | //Distance drop off for start of

anomaly in SONAR()
//SONAR SCANNING
#define NUMBER_OF_ANGLES_CHECKED | 15 | //Number of angles in SONAR sweep

//CAN ALIGN
#define INITIAL_CAN_ALIGN_SEC | 0 | //Time to re-adjust from initial

detection and parallel
#define INITIAL_CAN_ALIGN_MS | 900

#define SECONDARY_CAN_ALIGN_SEC 1 | //Time to re-adjust after approached

can but at a bad angle
#define SECONDARY_CAN_ALIGN_MS 100

//CAN APPROACH
#define FACE_CAN_ANGLE_TOLERANCE | 100 | //Directly facing tolerance (In servo

PWM period ~15 degrees)
#define FACE_CAN_DIST_TOLERANCE | 600 | //Distance away tolerance (Ultrasonic

pulse length ~6 cm)
#define CAN_APPROACH_SPEED | 40 | //Speed when approaching

//REVERSE TIME FOR RUN UP TO CAN
#define REVERSE_TIME | 750 | //750 ms reverse

//HIT CAN
#define HIT_TIME | 900 | //Time to drive into can for

## 6 Troubleshooting

This section of the document gives a step-by-step guide of how to find a broken element and repair it

should anything fail, or the cars behaviour becomes unexpected. This includes running individual

hardware test procedures on the MSP430, electrical continuity tests and examining expected signals at

different points of the system. The expected order and flow of the testing performed to find the fault

can be seen in Figure 36. All tests beyond running the hardware tests will require a multimeter and an

oscilloscope as well as some disassembly of the car.

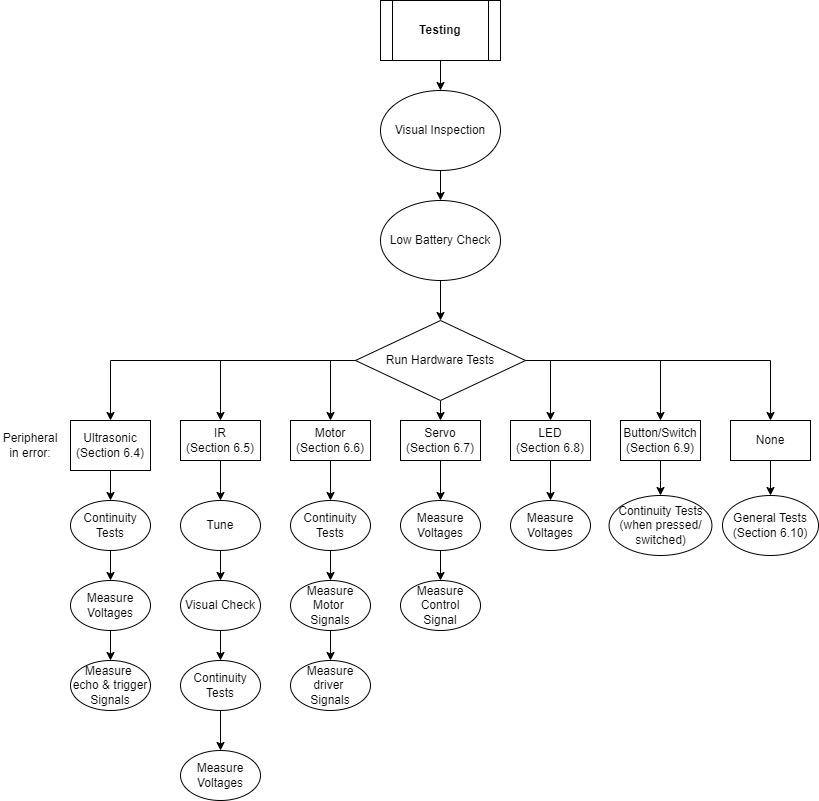
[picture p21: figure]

Figure 36: Expected flow of testing

## 6.1 Visual Inspection

If the car has stopped functioning as expected, the first check is to visually inspect the full car to see

any wiring harnesses have become disconnected or any wires clearly broken. If a wire is broken, follow

the instructions in Section 3.2.2 to construct a replacement wiring harness. Another visual check is the

power LEDs on the 3.3 V regulator and motor driver modules. Both should be illuminated whenever

the car is switched on. If not, check the connections between the battery and control board. On power

up, one of the indicator LEDs on top should be illuminated. If this is not the case, continue to the

hardware tests to find the issue.

## 6.2 Low Battery Check

If the low battery indicator LED on the control panel is lit when car is first turned on then the batteries

are low. If this is the case, then the batteries should be removed and recharged. Note that due to large

power draw and transients created from moving motors and servos the low battery indicator will flash

when car is running. This is not an indicator of low battery. The low battery indicator should only be

checked when car is first turned on. In case of failure of the low battery indicator circuit, the voltage

across the battery itself can be measured with a multimeter between the metal contacts highlighted in

Figure 37. Remember to remove the hot glue (added to ensure robustness). The nominal voltage is

roughly 4.8 V with a minimum operating voltage of 4.3 V and a fully charged maximum voltage of

5.33 V.

Figure 37: Battery Voltage Measurement Points

## 6.3 Hardware Tests

If the visual and battery checks do not reveal any issues, then the next stage is the hardware tests which

should be programmed on to the control board. These test every one of the peripherals connected to the

control board individually. The hardware tests (along with the main code) can be downloaded from the

GitHub (EE579-Skittles/HardwareTests/). Note that the main code (EE579-Skittles/CarReorganised/)

will also be required after testing so that it can be reprogrammed onto the car again once any issues are

resolved. The tests work by programming the onboard MSP430 with one at a time in a specific order.

The test that will be run is determined by the setup of the ‘HardwareTests/main.c’ file.

The functionality of each individual peripheral is stored within header and source files. Each file is

usually titled with the component name, such as ‘Servo.h’ and ‘Servo.c’ for the servo motor. The

‘Common.h’ and ‘Common.c’ files lay out everything required for an operating system and sets up

common elements such as timers and the structures such as flags, such that the main.c source file has

the highest level interface for user ease.

For the onboard MSP430 to be programmed with the hardware tests, a programmer is required to be

connected to the Control Board. A simple wiring harness is provided to connect the MSP43G2ET

development board to the Control Board as the programmer. Before connecting, ensure that the car is

switched off and that all LEDs are off. The car should not be disassembled for these tests. The wiring

harness with the required connections to the PCB and development board can be seen in Figure 38.

Ensure correct orientation regarding position of red wire. As previously stated, the red wire is connected

to VCC and in the case of the development board this is 3.3 V.

Figure 38: Wiring harness (left), Programmer PCB connection (middle) and dev. board connection (right)

Once the development board is connected to the car’s control board, and the development board

connected to a computer, the hardware tests can be uploaded. Using Code Composer Studio (CCS) or

some other appropriate IDE, the main function within the ‘main.c’ file can be edited to select the test to

be run as seen in Code Extract 2. These tests should be run in numerical order as many of the hardware

tests are dependent on the correct operation of other peripherals and so these need to be tested first.

Code Extract 2: Hardware Tests main.c file

// Enter 1 for indicator LEDs test // Enter 2 for start button test // Enter 3 for slide switch
// Enter 4 for drive test
// Enter 5 for steer test
// Enter 6 for servo test
// Enter 7 for SONAR ultrasonic test // Enter 8 for LEFT ultrasonic test // Enter 9 for RIGHT ultrasonic test // Enter 10 for Infrared test

selectComponent(1);

Changing the value within the ‘selectComponent()’ function selects the current test. Once selected it

can be uploaded to the car. The following section details the expected operation of each test if

component is fully working. Note that tests 4 – 9 require the car to be switched on after the car is

programmed due to the components under test requiring battery voltage level of nominal 4.8 V.

If the control board cannot be programmed, first check that all connections are correct, that the car

battery is switched off (note that power from the programmer will cause the control board to power up).

If still errors are being thrown by CCS, remove the MSP430 IC from the control board (noting

orientation) and place directly into the development board socket. Remove programming header,

reattach jumpers and attempt to program. If still errors are thrown, it can be confidently concluded that

the MSP430 is broken and will require replacement. If no errors, perform continuity tests of the

programming wiring harness. If this is found to be broken, replace according to 3.2.2.

A short description and the expected results of each test are listed below in running order:

1. LED Indicators: This test ensures both red and blue indicator LEDs on top of the car are

operating correctly. These LEDs are used for most other tests. When the test is run both LEDs

should illuminate.

2. Start Button: This test ensures that the start button on the control panel works. Pressing the

start button will toggle the red and blue indicator LEDs.

3. Slide Switch: This test ensures that the side select switch operates, where sliding it left will turn

the red LED on and sliding it right will illuminate the blue LED.

4. Drive: This test ensures that rear drive motor can turn forwards, backwards and stop. There are

two speeds, with the faster speed indicated by the blue LED and the slower speed indicated by

the red LED. The wheels should switch between running forwards and backwards at two

different speeds. For this test remember to lift the rear wheels from the ground to ensure the car

does not drive off. Ensure to switch on the car using the underside switch after programming the

test to the car.

5. Steer: This test ensures that front motor controlling steering works and does this by switching

between turning left, right, and straight continuously. This test also requires the car to be

switched on.

6. Servo: This test ensures that the servo motor for the top ultrasonic sensor works, where the servo

will continually move from one rotational limit to the other. This test requires car to be powered.

7. SONAR (top ultrasonic): All ultrasonic tests from 7 to 8 test use the same methods to test

different ultrasonic sensors. The LED indicator(s) will illuminate when the ultrasonic trigger

pulse is transmitted and is turned off when the ultrasonic sensor returns an echo pulse. For the

top ultrasonic, both the red and blue indicator LEDs are flashed to show functionality. The

ultrasonic is only triggered again after a pulse has been returned. This test requires car to be

switched on. If the LED illuminates but never switches off, this could be an indicator that either the ultrasonic is not receiving the trigger, the sensor is broken or that it is working and the echo

pulse is not received.

8. Left ultrasonic: See 7 for expected operation. For the left ultrasonic, the red indicator LED is

used to show functionality.

9. Right ultrasonic: See 7 for expected operation. For the right ultrasonic, the blue indicator LED

is used to show functionality.

10. Infrared: This checks the operability of the IR sensor. It illuminates both indicator LEDs if it

detects a white skittle and turns them both off if a black skittle or nothing is present. This can be

tested by placing any white or black object in front of the IR sensor. Note that one of the LEDs

on the IR sensor itself (see Figure 11) should match the indicator LED (ignoring the IR sensor

power LED). If they match yet are not switching as expected when shown a black or white object

then this could indicate the IR sensor requires tuning (see Section 6.5). If the on chip and

indicator LEDs do not light under the same conditions this could indicate a broken wiring

harness.

If the hardware tests reveal an inoperable peripheral, then continue on to the appropriate section of the

document for further testing. If no tests reveal an issue, attempt to reupload the main running code as

the car peripherals should be entirely functional.

## 6.4 Ultrasonic Error Diagnosis

The procedure for testing is the same for all three ultrasonic sensors. The first test is to measure the

supply voltage at the sensor itself. This will require removal of the sensor from the mounting. Refer to

Section 3.2.1 for how to do this. The voltage can be measured between the Vcc and GND pins

previously shown in Figure 9. This should give a value ranging from ~4.3 V to 5.3 V. If not, then the

ultrasonic is not powered correctly. This leads onto the continuity/resistance tests which check that the

wiring harness has not broken. This test will require full disassembly of the car and removal of the

control board. Once control board is removed, reattach the ultrasonic wiring harness and battery power

source. The continuity/resistance should be measured from the pins on the reverse of the control board

to the pins of the ultrasonic sensor itself, matching up the equivalent pins and expected resistance as in

Table 4. Note that the control board has a mis-labelled pin which has been corrected in Figure 39. The

schematic for the control board can be found in Appendix 11.1 to assist in understanding.

Table 4: Ultrasonic Testing expected resistances

PCB | Ultrasonic | Expected Resistance
BAT+ | Vcc | 0
Tr-X | Trigger | 0
Ec-X | Echo | ~470 Ω
GND | GND | 0

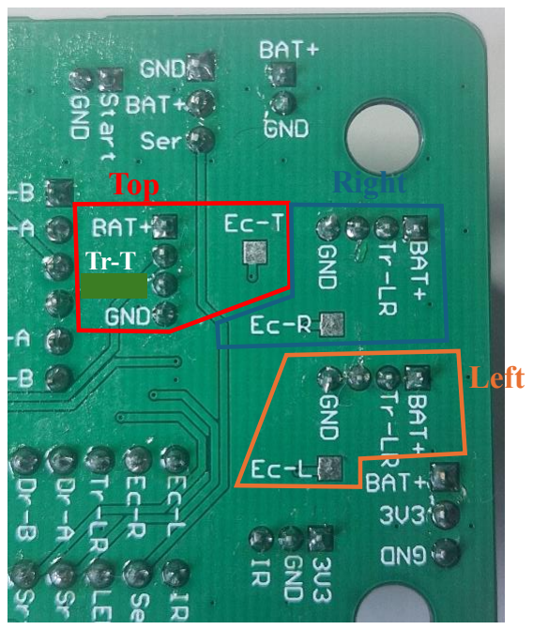
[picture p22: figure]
Top; Right; Left

Figure 39: Ultrasonic connections on control board

Should any of these test result in unexpected values, then the wiring harness should be replaced

following the steps in Section 3.2.2.

If no issues are found at this stage, testing is progressed to measuring the signals with an oscilloscope.

First the control board must be loaded with the hardware test for the specific ultrasonic.

To check the ultrasonic is being triggered correctly an oscilloscope should be connected to the trigger

pin directly on the ultrasonic sensor. The appropriate ultrasonic Hardware Test should be loaded onto

the MSP for that ultrasonic sensor. The oscilloscope should be connected before powering the car as

each consecutive trigger pulse is dependent on receiving the echo of the previous; therefore, if it is not

working only one pulse seen shortly after power up will be visible. A square pulse of approximately 20

µS should be viewed with an amplitude of about 3.3 V as seen in Figure 40. This means that the

ultrasonic is correctly triggered. If not witnessed, measure at the trigger pin on control board to

determine if wiring harness is at fault.

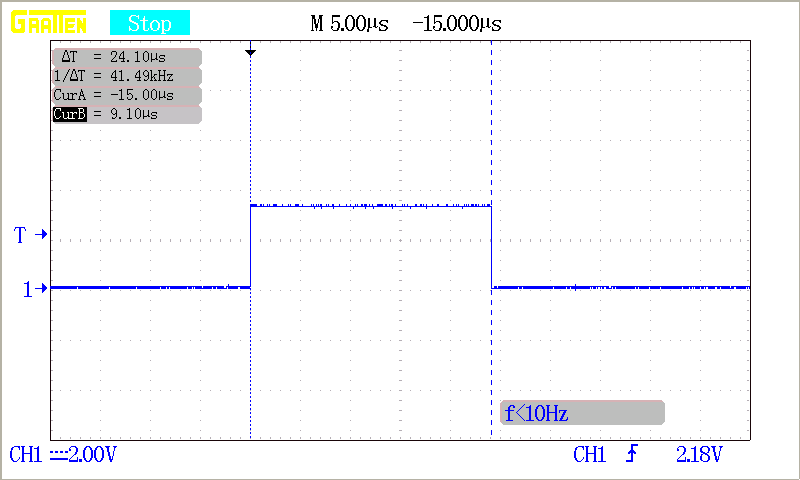
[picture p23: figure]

Figure 40: Expected Ultrasonic Trigger waveform

Next the echo signal should be verified by connecting the oscilloscope directly to the sensor. This test

should be performed with the sensor under test pointed towards a flat faced object roughly 30 cm away

relating to a pulse length of approximately 1.85 ms. The echo signal measured at the sensor should be

approximately as seen in Figure 41. If this is not observed, then the sensor itself is likely at fault and

should be replaced. The echo pulse should also be viewed to be the same when measured at test point

“Ec-X” (where X is T:top, L:left or R:right) on control board except of a lower amplitude of

approximately 3 to 3.3 V.

Figure 41: Expected ultrasonic echo waveform at sensor (left) and on control board (right)

## 6.5 Infrared (IR) Error Diagnosis

If the IR sensor is found to be at fault the first step is to check that the power LED is illuminated on the

sensor (see Section 3.1.2) when the car is powered. If not the voltage between Vcc and GND pins on

the sensor should be measured. If this is measured to be ~3.3 V then the sensor is broken and should be

replaced.

If the sensor is correctly powered, then the calibration of the sensor should be checked. Powering the

car up and placing white and matt black objects in front of the sensor, the LED onboard the sensor (see

Section 3.1.2) should light when presented with a white object and turn off when a black object is placed

in front. If this is not the case, the potentiometer on the sensor can be adjusted. Turning clockwise

increases sensitivity and anti-clockwise decreases sensitivity.

Ambient light will reduce the effective range of the sensor and can stop it functioning altogether. If the

sensor cannot differentiate between white and black objects, there is likely too much ambient light.

Electrical tape has been wrapped around the receiver to reduce these effects but further shrouds to block

the light could be constructed if ambient light is causing complications.

If the sensor’s onboard LED is seen to illuminate correctly yet the car’s indicator LEDs do not match it

then the wiring harness connection from the sensor to the control board is likely at fault so continuity

between the sensor and reverse of control board should be measured to verify this with a similar

procedure to the ultrasonic sensor. If this is the fault then the wiring harness can be replaced following

the procedure in Section 3.2.2.

## 6.6 Motor Error Diagnosis

If the one of the motors are found not to turn in hardware tests the likely issues are a broken connection

or a faulty motor driver. To tell if it is a fault wire, continuity test between the motor metal tabs (after

removing hot glue support) and the output connections on the PCB seen in Figure 42 should be

completed. If this is the issue, either the harness will need to be replaced and/or resoldered to the motor.

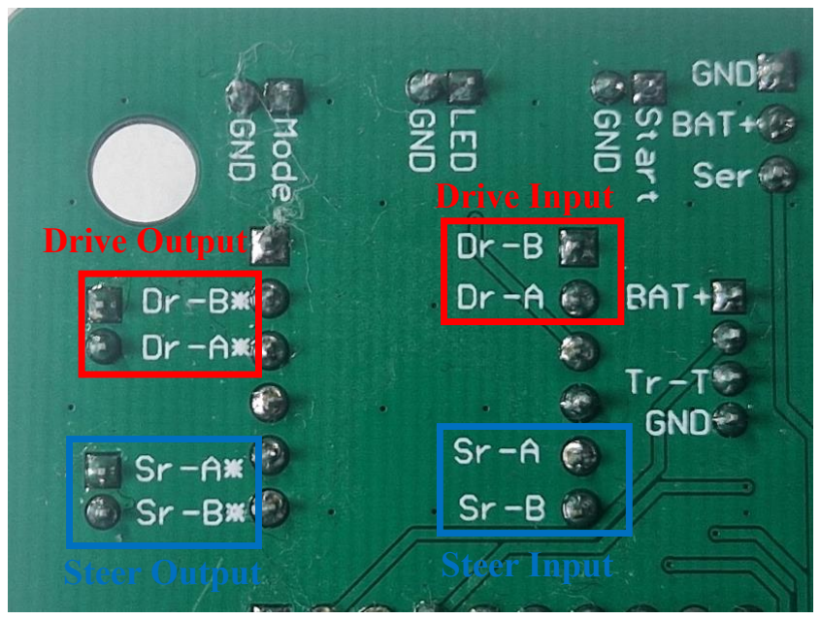
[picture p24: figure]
Steer Output; Drive Output; Drive Input; Steer Input

Figure 42: Motor driver control panel test points

If this is not the issue, it is likely the motor driver at fault. This can be verified by using an oscilloscope

to measure the PWM (Pulse Width Modulation) signal input to the motor driver and at the output. After

loading the MSP430 with the motor hardware test, lifting the wheels from the ground and powering the

car, the signals can be measured. The signal can be measured at the test points input to the motor driver

as highlighted in Figure 42. The expected waveforms at the two different speeds with measured pulse

widths can be viewed in Figure 43. The pulse period is approximately 50 ms for this test.

Figure 43: Motor PWM Control signal waveform

A signal like this should also be measured on the control panel at the motor driver output test points

except likely with more noise, transients and at about 4.8 V rather than 3.3 V. If the output signal cannot

be seen as expected, then the motor driver is at fault and should be replaced. Due to the nature of the

design the motor driver can simply be pulled out to be replaced.

## 6.7 Servo Error Diagnosis

If the servo is not turning as expected, the first check is to measure the supply voltage between BAT+

and GND on the PCB as highlighted in Figure 44. The voltage measured is expected to be between

approximately 4.3 V and 5.33 V. If this is not as expected, then the battery or connection to battery is

likely the issue.

Figure 44: Servo test points on control panel

The next stage is to measure the PWM servo control signal if the supply voltage is acceptable. The

servo hardware test should be uploaded which should make the servo turn from maximum to minimum

limit continuously. The expected pulse widths to be measured on the control board test point (Ser) at

maximum and minimum angles can be seen in Figure 45.

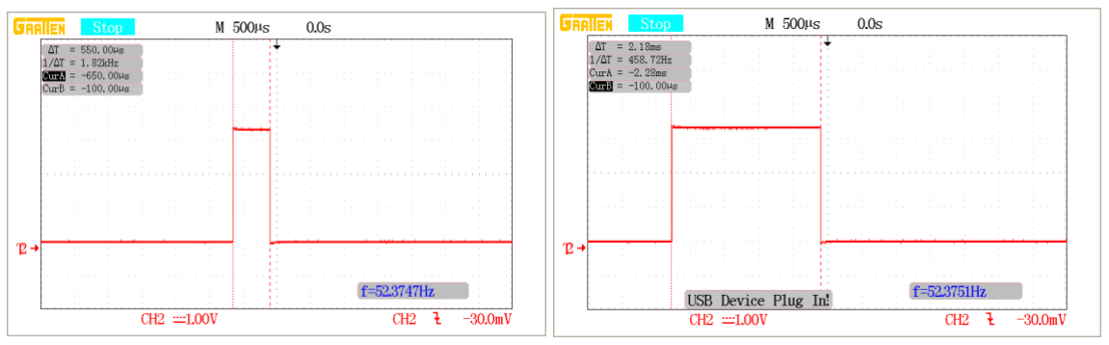
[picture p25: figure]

Figure 45: Servo PWM control signal at maximum and minimum angle

If these pulses are as expected and yet the servo still is not turning then the servo is likely at fault and

should be replaced.

## 6.8 Indicator LED Error Diagnosis

If the indicator hardware tests reveal an issue with the LEDs, then the voltage should be measured to

be non-zero between the two pins of each LED set of pins when the hardware test is loaded. This

indicates that the LED or wires are broken, due to the nature of its construction it would be more

efficient to remake the full LED harness with a new LED.

## 6.9 Button/Switch Error Diagnosis

If the hardware tests reveal an issue with the start button or side select switch, then they should be

quickly continuity tested. To do this unplug from the control panel and continuity test between the two

points on the button/switch harness connector while pressing/switching. Continuity should be achieved

for the start button while it is pressed and for the side select switch when it is switched to only one side

not the other. If continuity check reveals that the button or switch is non-functional, they should be fully

replaced with a new button/switch and harness. If they are functional, reconnect to the board as it could

have been an unsecure connection.

## 6.10 General Error Diagnosis

If the control board can be programmed but does not function when powered from the car, then the 3.3

V voltage regulator is likely at fault. It is very simple to remove and replace with a new regulator.

Another major fault to check for is a short between VCC and GND. This will cause the car to not

function and not be able to be reprogrammed. This should be checked at both BAT+ and 3V3 to GND

as these are separated by the voltage regulator. GND is common to everywhere however.

## 7 Design Validation

RUSH’s complete functionality was validated with a demo in competition with nine other competing

cars. Each team competed in two heats with the teams with the lowest four combined times to hit black

skittles to progress to the semi-finals. In the first heat the car won by hitting a black skittle first. The

second heat was lost as the opposing team hit a black can first however RUSH still hit the black skittle.

RUSH reached the black skittle first but due to the slow SONAR sweep it was last to knock it over.

This highlighted how much improving the SONAR sweep would improve the speed of the car. With the

lowest combined time from the heats, RUSH proceed to the semi-finals where it won by hitting a black

can directly in front in 8 s. It was this quick due to the car not entering search mode in time for the black

to be detected. For the final, no skittles were knocked over by either team, with RUSH winning due to

larger displacement from the start line. This was due to no skittle being detected as during calibration

the users’ setup the calibration walls too close for the skittle to be detected. Due to the anti-climactic

nature of the final a second final was held in which RUSH detected and dealt with all three skittles. It

encountered the white first and avoided it and then went on to knock down the two black skittles.

However, some assistance was required to remove an already knocked black can as it was detecting this

in the SONAR sweep and could not therefore get to the next can.

Throughout each game, RUSH was proven to be very consistent and robust, able to get to a black skittle

almost every time (given that it was correctly calibrated by the users). The wall alignment performed

very well and was able to keep the car very straight down the corridor. Details on possible future

improvements that could solve some of the issues encountered in the demo are covered in Section 9.

## 8 Summary

This technical documentation file has covered all aspects of the hardware (Section 3) and software

functionality (Section 4) of RUSH. Disassembly instructions have been presented in Section 3.2.1

should anything break or future improvement listed in Section 9 be implemented. The primary variables

that can be altered to tune RUSH’s performance was detailed in Section 5. Full instructions on the steps

of testing that should be taken if RUSH behave expectedly (conflicting with the expect functionality

described in Section 4.1) or break entirely was shown in Section 6. RUSH’s design was validated to be

robust and very consistent with the results of testing in Section 7. For any more details including full

code listing, CAD designs, hardware tests, BoM and videos of operations refer to the GitHub repository

(https://github.com/Ross1416/EE579-Skittles).

## 9 Future Improvements

Although RUSH operates well, there are a number of improvements that could be made to the car that

would make it faster and more reliable. This section details the primary improvements that would likely

make the most impact and were not explored for RUSH’s development due to time constraints and the

aim to keep costs low.

## 9.1 Improved Scanning Sweep

From extensive testing, the primary improvement would be to replace the top ultrasonic sensor with an

alternative with a smaller detection scope. This would improve RUSH’s ability to locate skittles in the

SONAR scan state and its reliability in staying locked on to a skittle whilst navigating towards it. It

would allow determination of the exact centre of the skittle resulting in a higher accuracy in positioning

the IR colour sensor face on with the skittle. It would also increase its ability to differentiate between

skittle and walls. A possible alternative that would meet this criterion would be a Time-of-Flight sensor

(ToF) which uses pulses of laser light to determine range. This beam would be very narrow and therefore

have a very small detection scope as seen in Figure 46.

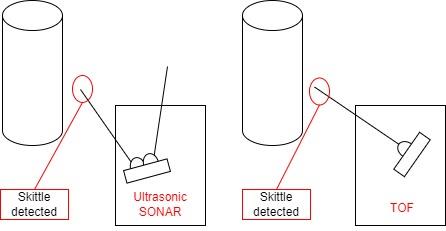
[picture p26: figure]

Figure 46: Skittle detection with Ultrasonic and Time of Flight (TOF)

The main sensor used by competing cars is the ultrasonic sensor and therefore use of the ToF sensor

would also negate any possible interference caused by competitor’s cars. Interference wasn’t found to

be a large issue, however, it was tested to be possible. ToF sensors commonly take advantage of the I2C

communication protocol. This would increase the complexity of the main code for the MSP430 but it

does contain functionality for I2C communication. A large issue however would be that this

functionality operates on specific pins which may require a different MSP package and/or reworking of

the pins already used which would have further implications on the designed PCB. With the original

top ultrasonic sensor also performing the job of detecting objects in front of the car whilst searching,

the ToF sensor would not perform as well. It would not detect skittles slightly off centre of the car and

allow the car to strike skittles without realising it. Therefore, a stationary mounted ultrasonic or

equivalent with a wide detection scope would likely still be required.

Another similar issue noticed with the ultrasonic sensors was that skittles that had been knocked over

would still be detected and therefore cause the car to attempt to manoeuvre towards an already knocked

skittle. A simple fix for this would be to either tilt the sensors up slightly or redesign the structure to

raise them up to a point knocked cans will no longer be detected.

## 9.2 Realignment

Another issue noted in testing was the way the car attempted to reposition after dealing with a skittle.

The realignment procedure uses set times and directions depending on original detection of the skittle.

If the car ends up facing an unexpected direction, then this realignment has failed. This is not too

important should the car have reached and dealt with a black can. Should the black skittle be positioned

behind a white can however this could pose an issue. A possible solution to know where the car is in

the space and in what direction it is facing could be an IMU (Inertia Measurement Unit) which contain

accelerometer, gyroscope and magnetometer. The IMU could also assist in other operations such as

driving straight and aid the wall alignment with side ultrasonic sensors. The drawback of this method,

similar to ToF, is that I2C would have to be implemented for the IMU’s and likely cause large redesign

implications.

## 9.3 Improved steering

RUSH’s steering mechanism is unaltered from the base RC car. It relies on a DC motor and only allows

turning left, right (by about 60°) or straight. The mechanism itself its very loose and allows a lot of play

in the steering; this translates to the car struggling to drive straight. Since the game rules allow

modification to the steering, this whole mechanism could be redesigned to reduce the play and use a

servo or stepper motor instead. This would allow accurate control of the angle of the wheels and not

just left or right. The steering angle could also possibly be increased therefore reducing the turning

radius of the car. This improved steering could be paired with the IMU and possibly a form of PID

(Proportional Integral Differential) controller to allow car to drive straight. This would allow the speed

of the car to be increased at least in the initial sprint mode.

## 9.4 Pre-game Search Mode

The rules stipulate that in the minute before the game of skittles start, both teams can view the position

of the skittles in the play area. RUSH does not exploit this, however many possibilities of doing this

were proposed. One possibility would be for the car, in the minute preparation time before the start,

race down the centre of the track and note the positions of all skittles before returning to the start line.

The user could then input the colour of cans in the order of detection via buttons on the control panel.

On start up the car could then move directly towards the first black skittle since it already has knowledge

of its position. This would cause issues in ensuring that the car returns to the start line before the minute

has elapsed. The functionality of this would be simple to integrate with the software structure and PCB

design as it is. In software the needed states to achieve this can be easily added and will work

independently of other states just need to add the entry and exit points at the right time for functionality.

In hardware there is a port already setup for an additional button which could operate as the black /

white input and that GPIO is currently unused in code.

## 9.5 Improved Power source

The power source of RUSH was chosen due to simple integration into the base RC car and that it only

required a single step-down linear voltage regulator to be paired with it for the car to function. This

source had a number of drawbacks however. Since the battery voltage is not entirely consistent and

varies from about 5.33 V to 4.3 V, where the car will begin to fail, the speed of the car varies. This is

seen to be significant when not operating in the relatively consistent 4.8 V nominal region of discharge.

This causes some issues as a large amount of the manoeuvring depends on timings and if the motors

run at different speeds this results in a difference in movements. This could, alternatively, be solved by

a sensor for motor wheel speeds and update timings accordingly. However, a combination of alternative

sources and regulators/convertors could be used to achieve a stable 5V VCC to maintain consistent

motor speed. Lithium Ion (Li-Ion) batteries could be exploited for their higher energy density; however

these batteries pose safety concerns and would likely require additional protection systems. It would

allow, with some additional circuitry, simple charging of the battery within the car, improving overall

useability. Any alterations made to the battery/power source should ensure that the weight is evenly

distributed as the batteries for RUSH are unevenly distributed and causes the car to drift right slightly

with the weight of the externally mounted NiMH battery.

The low battery indicator could also be improved to stop the flashing of the LED when the car is moving.

A simple solution could possibly be to add some capacitors for some small energy storage and smooth

out any transients.

## 10 References

[1] Argos, “BMW i8 1:24 Radio Controlled Sports Car,” Argos, [Online]. Available:

https://www.argos.co.uk/product/7655915?clickSR=slp:term:rc%20car:1:39:1. [Accessed

02 05 2024].

[2] “Texas Instruments MSP430G2553IN20, 16bit MSP430 Microcontroller, MSP430,

16MHz, 16 kB Flash, 20-Pin PDIP,” RS Components, [Online]. Available: https://uk.rs-

online.com/web/p/microcontrollers/8176411?gb=s . [Accessed 05 05 24].

[3] “Texas Instruments MSP-EXP430G2ET Development Kit,” Mouser, [Online]. Available:

https://www.mouser.co.uk/new/texas-instruments/ti-msp-exp430g2et-dev-kit/. [Accessed

05 05 2024].

[4] “DRV8833 Dual H-Bridge Motor Driver Module,” Components101, [Online]. Available:

https://components101.com/modules/drv8833-dual-h-bridge-motor-driver-module.

[Accessed 05 05 24].

[5] “How does a Servo Motor Work and How to Interface it with ESP32?,” CircuitDigest,

[Online]. Available: https://circuitdigest.com/microcontroller-projects/interfacing-sg90-

servo-motor-with-esp32 . [Accessed 05 05 25].

[6] S. Vorkoetter, “Choosing and Using Nickel-Metal-Hydride (NiMH) Rechargeable

Batteries,” [Online]. Available: http://www.stefanv.com/electronics/using_nimh.html.

[Accessed 04 05 24].

[7] “Make | a | Good | Dupont | Pin-Crimp | EVERY TIME!,” | [Online]. Available:

https://www.instructables.com/Make-a-Good-Dupont-Pin-Crimp-EVERY-TIME/.

[Accessed 05 05 24].

[8] Texas Instruments, “MSP430G2x53 Datasheet,” Texas Instruments Incorporated, Dallas,

2013.

[9] Texas Instruments, “MSP430F2xx, MSP430G2xx Family: User’s Guide,” Texas

Instruments Incorporated, Dallas, 2022.

45

## 11 Appendix

## 11.1 PCB Schematic

*BLACK button was unused, instead blue indicator LED; WHITE was unused entirely.

46

## 11.2 Bill of Materials (BoM)

Component ID | Name | Type | Quantity | PCB Designator(s) | Package | Manufacturer | Manufacurer Part Number | Distributer | Distributer Stock Number

Individual Cost (inc VAT)
(£) | Total Cost (£) | Note
E-01 | MSP430G2553 | Microcontroller | 1 | - | DIP-20 | Texas Instruments | MSP430G2553IN20 | RS | 817-6411 | £2.802 | £2.802 Free from Lab
E-02 | 20-pin IC socket | IC Socket | 1 | J8 | DIP-20 | Winslow | W3120TRC | RS | 402-793 | £0.143 | £0.143
E-03 | 2-pin JST PH2.0 Header | Header | 9 | J4,J5,J9,J10,J12,J13,J14,J15,J16 | 2mm THT | JST | B2B-PH-K-S(LF)(SN) | RS | 166-7311 | £0.068 | £0.612
E-04 | 3-pin JST PH2.0 Header | Header | 1 | J17 | 2mm THT | JST | B3B-PH-K-S(LF)(SN) | RS | 820-1431 | £0.046 | £0.046
E-05 | 4-pin JST PH2.0 Header | Header | 3 | J3,J6,J11 | 2mm THT | JST | B4B-PH-K-S(LF)(SN) | RS | 172-4893 | £0.118 | £0.354
E-06 | 3-pin Dupont Male Header | Header | 1 | J7 | 2.54mm THT | Wurth Elektronik | 61300311121 | RS | 172-5145 | £0.070 | £0.070
E-07 | 3-pin Dupont Female Header | Header | 1 | J2 | 2.54mm THT | Wurth Elektronik | 61300311821 | RS | 233-9349 | £0.296 | £0.296
E-08 | 4-pin Dupnt Male Header | Header | 1 | J17 | 2.54mm THT | Wurth Elektronik | 61300411121 | RS | 172-5155 | £0.095 | £0.095
E-09 | 6-pin Dupont Female Header | Header | 2 | J18,J19 | 2.54mm THT | Wurth Elektronik | 61300611821 | RS | 205-3156 | £0.221 | £0.442
E-10 | AMS1117 Module | 3.3V Regulator Module | 1 | - | 2.54mm THT | - | - | Amazon | B0CV371GGF | £0.370 | £0.370
E-11 | DRV8833 Module | Motor Driver Module | 1 | - | 2.54mm THT | - | - | Amazon | B09Z2JV3LY | £1.198 | £1.198
E-12 | 470R Resistor | Resistor | 5 | R1,R2,R4,R7,R11 | 0805 | Bourns | CR0805-FX-4700ELF | RS | 161-6929 | £0.005 | £0.025
E-13 | 1k Resistor | Resistor | 4 | R10 | 0805 | Bourns | CR0805-JW-102ELF | RS | 167-4709 | £0.004 | £0.016
E-14 | 10k Resistor | Resistor | 1 | R5 | 0805 | Bourns | CR0805-FX-1002ELF | RS | 167-5121 | £0.005 | £0.005
E-15 | Zener Diode | Zener | 1 | Z1 | SOD-123 | onsemi | MMSZ5226BT1G | RS | 545-2989 | £0.115 | £0.115
E-16 | 10k Potentiometer | Potentiometer | 1 | R9 | - | Bourns | 3314G-1-103E | RS | 100-1177 | £1.564 | £1.564
E-17 | TS952IPT OP-AMP | Operational Amplifier | 1 | IC1 | TSSOP-8 | STMicroelectronics | TS952IPT | RS | 795-8694 | £0.850 | £0.850
E-18 | IR Sensor | Infrared Sensor | 1 | - | - | - | - | Amazon | B08BK4SB5W | £1.632 | £1.632
E-19 | HC-SR04 Ultrasonic Sensor Module | Ultrasonic Sensor | 3 | - | - | - | - | Amazon | B07XF4815H | £1.498 | £4.494
E-20 | SG-90 Servo | Servo | 1 | - | - | - | - | Amazon | B09FL1W3KM | £2.000 | £2.000
E-21 | Start Button | Push Button | 1 | - | - | Shin Chin | R13-510A-05-BR | Mouser | 112-R13-510A-R | £0.963 | £0.963 Free from Lab
E-22 | Side Select Switch | Switch | 1 | - | - | E-Switch | EG1201A | Mouser | 612-EG1201A | £0.610 | £0.610 Free from Lab
E-23 | NiMH Batteries (2400 mA) | Batteries | 4 | - | AA | Amazon | B08BK4SB5W | Amazon | B08BK4SB5W | £1.365 | £5.460
E-24 | 2-pin JST Connector Housing | Connector Housing | 5 | - | 2mm THT | JST | PHR-2 | RS | 166-7504 | £0.034 | £0.170
E-25 | 3-pin JST Connector Housing | Connector Housing | 1 | - | 2mm THT | JST | PHR-3 | RS | 820-1475 | £0.065 | £0.065
E-26 | 4-pin JST Connector Housing | Connector Housing | 3 | - | 2mm THT | JST | PHR-4 | RS | 820-1478 | £0.085 | £0.255
E-27 | JST PH Female Crimp | Female Crimp | 25 | - | - | JST | SPH-002T-P0.5S | RS | 166-7577 | £0.018 | £0.450
E-28 | Red LED | LED | 2 | - | 5mm THT | Lite-On | LTL-307E | RS | 168-9439 | £0.040 | £0.080 Free from Lab
E-29 | Blue LED | LED | 1 | - | 5mm THT | Wurth Elektronik | 151051BS04000 | RS | 146-0102 | £0.137 | £0.137 Free from Lab
E-30 | 470R Resistor | Resistor | 1 | - | THT | RS PRO | 739-7430 | RS | 739-7430 | £0.010 | £0.010 Free from Lab
E-31 | Single AA Battery Holder | Battery Holder | 1 | - | - | RS PRO | 512-3574 | RS | 512-3574 | £1.490 | £1.490
E-32 | 3-pin 2.54mm Connector Housing | Connector Housing | 1 | - | 2.54mm | HARWIN | M20-1060300 | RS | 173-0802 | £0.078 | £0.078
E-33 | 4-pin 2.54mm Connector Housing | Connector Housing | 2 | - | 2.54mm | HARWIN | M20-1060400 | RS | 173-0807 | £0.113 | £0.226
E-34 | 2.54mm Female Crimp | Female Crimp | 15 | - | - | HARWIN | M20-1180046 | RS | 681-2887 | £0.058 | £0.870
M-01 | Lower Mount | Mount | 1 | - | - | - | - | - | - | £0.000 M-02 | Upper Mount | Mount | 1 | - | - | - | - | - | - | £0.000 M-03 | Ultrasonic Mount | Mount | 3 | - | - | - | - | - | - | £0.000 M-04 | Ultrasonic Backplate | Mount | 3 | - | - | - | - | - | £0.000 M-05 | IR Lower Mount | Mount | 1 | - | - | - | - | - | - | £0.000 M-06 | IR Upper Mount | Mount | 1 | - | - | - | - | - | - | £0.000 M-07 | Servo Base Mount Left | Mount | 1 | - | - | - | - | - | - | £0.000 M-08 | Servo Base Mount Right | Mount | 1 | - | - | - | - | - | - | £0.000 M-09 | Servo Ultrasonic Mount | Mount | 1 | - | - | - | - | - | - | £0.000 M-10 | Control Panel Bottom | Mount | 1 | - | - | - | - | - | - | £0.000 M-11 | Control Panel Middle | Mount | 2 | - | - | - | - | - | - | £0.000 M-12 | Control Panel Top | Mount | 1 | - | - | - | - | - | - | £0.000 M-13 | M2x16 Bolt | Bolt | 6 | - | M2x16 | - | - | - | - | £0.000 M-14 | M2x12 Bolt | Bolt | 6 | - | M2x12 | - | - | - | - | £0.000 M-15 | M2x8 Bolt | Bolt | 3 | - | M2x8 | - | - | - | - | £0.000 M-16 | M2 Nut | Nut | 8 | - | M2 | - | - | - | - | £0.000 M-17 | M2 Washer | Washer | 5 | - | M2 | - | - | - | £0.000 M-18 | M2 Threaded Inserts | Threaded Inserts | 2 | - | M2 | - | - | £0.000 M-19 | Servo Screw | Screw | 1 | - | £0.000 Only Phillips head
Total | £27.993
E-01 | Base RC Car | Remote Controlled Car | 1 | - | - | Raster Toys | - | Argos | - | £12.000 | £12.000
E-02 | MSP-EXP430G2ET Dev Board | Development Board | 1 | - | - | Texas Instruments | MSP-EXP430G2ET | DigiKey | 296-50264-ND | £9.510 | £9.510 Extras Mounts Electronics

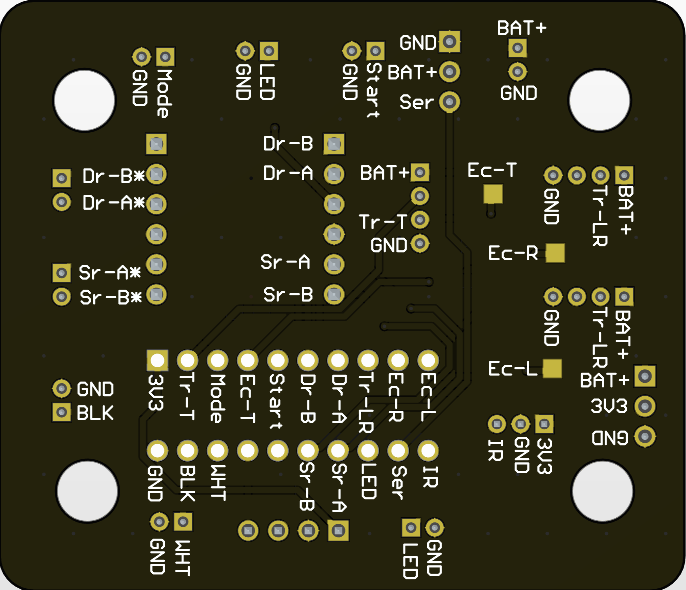
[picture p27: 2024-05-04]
CAD/PCB/PCB_bottom_decal.png

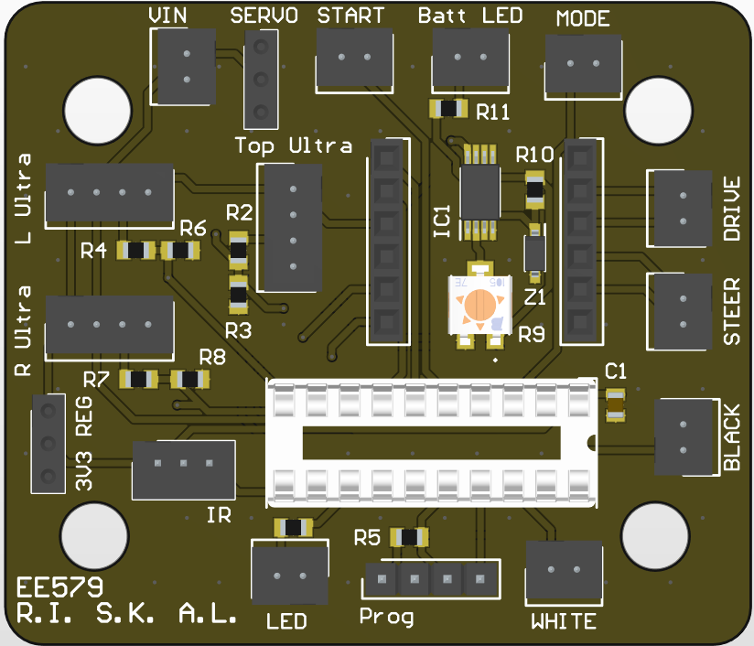
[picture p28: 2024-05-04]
CAD/PCB/PCB_top_decal.png

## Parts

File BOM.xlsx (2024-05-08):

 | Component ID | Name | Type | Quantity | PCB Designator(s) | Package | Manufacturer | Manufacurer Part Number | Distributer | Distributer Stock Number | Individual Cost (inc VAT) (£) | Total Cost (£) | Note | Link
Electronics | E-01 | MSP430G2553 | Microcontroller | 1 | - | DIP-20 | Texas Instruments | MSP430G2553IN20 | RS | 817-6411 | £2.802 | £2.802 | Free from Lab | https://uk.rs-online.com/web/p/microcontrollers/8176411?gb=s
 | E-02 | 20-pin IC socket | IC Socket | 1 | J8 | DIP-20 | Winslow | W3120TRC | RS | 402-793 | £0.143 | £0.143 |  | https://uk.rs-online.com/web/p/dil-sockets/0402793?gb=s
 | E-03 | 2-pin JST PH2.0 Header | Header | 9 | J4,J5,J9,J10,J12,J13,J14,J15,J16 | 2mm THT | JST | B2B-PH-K-S(LF)(SN) | RS | 166-7311 | £0.068 | £0.612 |  | https://uk.rs-online.com/web/p/pcb-headers/1667311?gb=s
 | E-04 | 3-pin JST PH2.0 Header | Header | 1 | J17 | 2mm THT | JST | B3B-PH-K-S(LF)(SN) | RS | 820-1431 | £0.046 | £0.046 |  | https://uk.rs-online.com/web/p/pcb-headers/8201431?gb=s
 | E-05 | 4-pin JST PH2.0 Header | Header | 3 | J3,J6,J11 | 2mm THT | JST | B4B-PH-K-S(LF)(SN) | RS | 172-4893 | £0.118 | £0.354 |  | https://uk.rs-online.com/web/p/pcb-headers/1724893?gb=s
 | E-06 | 3-pin Dupont Male Header | Header | 1 | J7 | 2.54mm THT | Wurth Elektronik | 61300311121 | RS | 172-5145 | £0.070 | £0.070 |  | https://uk.rs-online.com/web/p/pcb-headers/1725145
 | E-07 | 3-pin Dupont Female Header | Header | 1 | J2 | 2.54mm THT | Wurth Elektronik | 61300311821 | RS | 233-9349 | £0.296 | £0.296 |  | https://uk.rs-online.com/web/p/pcb-sockets/2339349
 | E-08 | 4-pin Dupnt Male Header | Header | 1 | J17 | 2.54mm THT | Wurth Elektronik | 61300411121 | RS | 172-5155 | £0.095 | £0.095 |  | https://uk.rs-online.com/web/p/pcb-headers/1725155
 | E-09 | 6-pin Dupont Female Header | Header | 2 | J18,J19 | 2.54mm THT | Wurth Elektronik | 61300611821 | RS | 205-3156 | £0.221 | £0.442 |  | https://uk.rs-online.com/web/p/pcb-sockets/2053156
 | E-10 | AMS1117 Module | 3.3V Regulator Module | 1 | - | 2.54mm THT | - | - | Amazon | B0CV371GGF | £0.370 | £0.370 |  | https://www.amazon.co.uk/YINETTECH-AMS1117-3-3-Step-Down-Stabilization-Stabilizing/dp/B0CV371GGF
 | E-11 | DRV8833 Module | Motor Driver Module | 1 | - | 2.54mm THT | - | - | Amazon | B09Z2JV3LY | £1.198 | £1.198 |  | https://www.amazon.co.uk/Fasizi-DRV8833-2-Channel-Ultra-small-Voltage/dp/B09Z2JV3LY
 | E-12 | 470R Resistor | Resistor | 5 | R1,R2,R4,R7,R11 | 0805 | Bourns | CR0805-FX-4700ELF | RS | 161-6929 | £0.005 | £0.025 |  | https://uk.rs-online.com/web/p/surface-mount-resistors/1616929
 | E-13 | 1k Resistor | Resistor | 4 | R10 | 0805 | Bourns | CR0805-JW-102ELF | RS | 167-4709 | £0.004 | £0.016 |  | https://uk.rs-online.com/web/p/surface-mount-resistors/1674709
 | E-14 | 10k Resistor | Resistor | 1 | R5 | 0805 | Bourns | CR0805-FX-1002ELF | RS | 167-5121 | £0.005 | £0.005 |  | https://uk.rs-online.com/web/p/surface-mount-resistors/1675121
 | E-15 | Zener Diode | Zener | 1 | Z1 | SOD-123 | onsemi | MMSZ5226BT1G | RS | 545-2989 | £0.115 | £0.115 |  | https://uk.rs-online.com/web/p/zener-diodes/5452989?gb=s
 | E-16 | 10k Potentiometer | Potentiometer | 1 | R9 | - | Bourns | 3314G-1-103E | RS | 100-1177 | £1.564 | £1.564 |  | https://uk.rs-online.com/web/p/trimmer-potentiometers/1001177?gb=s
 | E-17 | TS952IPT OP-AMP | Operational Amplifier | 1 | IC1 | TSSOP-8 | STMicroelectronics | TS952IPT | RS | 795-8694 | £0.850 | £0.850 |  | https://uk.rs-online.com/web/p/op-amps/7958694?gb=s
 | E-18 | IR Sensor | Infrared Sensor | 1 | - | - | - | - | Amazon | B08BK4SB5W | £1.632 | £1.632 |  | https://www.amazon.co.uk/dp/B08BK4SB5W?psc=1&ref=ppx_yo2ov_dt_b_product_details
 | E-19 | HC-SR04 Ultrasonic Sensor Module | Ultrasonic Sensor | 3 | - | - | - | - | Amazon | B07XF4815H | £1.498 | £4.494 |  | https://www.amazon.co.uk/HC-SR04-Ultrasonic-Distance-Arduino-MEGA2560/dp/B07XF4815H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
 | E-20 | SG-90 Servo | Servo | 1 | - | - | - | - | Amazon | B09FL1W3KM | £2.000 | £2.000 |  | https://www.amazon.co.uk/ALMOCN-Helicopter-Aeroplane-Compatible-Raspberry/dp/B09FL1W3KM
 | E-21 | Start Button | Push Button | 1 | - | - | Shin Chin | R13-510A-05-BR | Mouser | 112-R13-510A-R | £0.963 | £0.963 | Free from Lab | https://www.mouser.co.uk/ProductDetail/Shin-Chin/R13-510A-05-BR?qs=F3UvtXhGJLMNVkQjXJ4Pyw%3D%3D
 | E-22 | Side Select Switch | Switch | 1 | - | - | E-Switch | EG1201A | Mouser | 612-EG1201A | £0.610 | £0.610 | Free from Lab | https://www.mouser.co.uk/ProductDetail/E-Switch/EG1201A?qs=HKd%2Fp3M7KlUl1Yo84njqrQ%3D%3D
 | E-23 | NiMH Batteries (2400 mA) | Batteries | 4 | - | AA | Amazon | B08BK4SB5W | Amazon | B08BK4SB5W | £1.365 | £5.460 |  | https://www.amazon.co.uk/dp/B00HZV9WTM/ref=twister_B0BYP91DQS?_encoding=UTF8&psc=1
 | E-24 | 2-pin JST Connector Housing | Connector Housing | 5 | - | 2mm THT | JST | PHR-2 | RS | 166-7504 | £0.034 | £0.170 |  | https://uk.rs-online.com/web/p/wire-housings-plugs/1667504?gb=s
 | E-25 | 3-pin JST Connector Housing | Connector Housing | 1 | - | 2mm THT | JST | PHR-3 | RS | 820-1475 | £0.065 | £0.065 |  | https://uk.rs-online.com/web/p/wire-housings-plugs/8201475?gb=s
 | E-26 | 4-pin JST Connector Housing | Connector Housing | 3 | - | 2mm THT | JST | PHR-4 | RS | 820-1478 | £0.085 | £0.255 |  | https://uk.rs-online.com/web/p/wire-housings-plugs/8201478?gb=s
 | E-27 | JST PH Female Crimp | Female Crimp | 25 | - | - | JST | SPH-002T-P0.5S | RS | 166-7577 | £0.018 | £0.450 |  | https://uk.rs-online.com/web/p/crimp-contacts/1667577?gb=a
 | E-28 | Red LED | LED | 2 | - | 5mm THT | Lite-On | LTL-307E | RS | 168-9439 | £0.040 | £0.080 | Free from Lab | https://uk.rs-online.com/web/p/leds/1689439
 | E-29 | Blue LED | LED | 1 | - | 5mm THT | Wurth Elektronik | 151051BS04000 | RS | 146-0102 | £0.137 | £0.137 | Free from Lab | https://uk.rs-online.com/web/p/leds/1460102
 | E-30 | 470R Resistor | Resistor | 1 | - | THT | RS PRO | 739-7430 | RS | 739-7430 | £0.010 | £0.010 | Free from Lab | https://uk.rs-online.com/web/p/through-hole-resistors/7397430
 | E-31 | Single AA Battery Holder | Battery Holder | 1 | - | - | RS PRO | 512-3574 | RS | 512-3574 | £1.490 | £1.490 |  | https://uk.rs-online.com/web/p/battery-holders/5123574?gb=s
 | E-32 | 3-pin 2.54mm Connector Housing | Connector Housing | 1 | - | 2.54mm | HARWIN | M20-1060300 | RS | 173-0802 | £0.078 | £0.078 |  | https://uk.rs-online.com/web/p/wire-housings-plugs/1730802
 | E-33 | 4-pin 2.54mm Connector Housing | Connector Housing | 2 | - | 2.54mm | HARWIN | M20-1060400 | RS | 173-0807 | £0.113 | £0.226 |  | https://uk.rs-online.com/web/p/wire-housings-plugs/1730807
 | E-34 | 2.54mm Female Crimp | Female Crimp | 15 | - | - | HARWIN | M20-1180046 | RS | 681-2887 | £0.058 | £0.870 |  | https://uk.rs-online.com/web/p/crimp-contacts/6812887
Mounts | M-01 | Lower Mount | Mount | 1 | - | - | - | - | - | - |  | £0.000
 | M-02 | Upper Mount | Mount | 1 | - | - | - | - | - | - |  | £0.000
 | M-03 | Ultrasonic Mount | Mount | 3 | - | - | - | - | - | - |  | £0.000
 | M-04 | Ultrasonic Backplate | Mount | 3 | - |  | - | - | - | - |  | £0.000
 | M-05 | IR Lower Mount | Mount | 1 | - | - | - | - | - | - |  | £0.000
 | M-06 | IR Upper Mount | Mount | 1 | - | - | - | - | - | - |  | £0.000
 | M-07 | Servo Base Mount Left | Mount | 1 | - | - | - | - | - | - |  | £0.000
 | M-08 | Servo Base Mount Right | Mount | 1 | - | - | - | - | - | - |  | £0.000
 | M-09 | Servo Ultrasonic Mount | Mount | 1 | - | - | - | - | - | - |  | £0.000
 | M-10 | Control Panel Bottom | Mount | 1 | - | - | - | - | - | - |  | £0.000
 | M-11 | Control Panel Middle | Mount | 2 | - | - | - | - | - | - |  | £0.000
 | M-12 | Control Panel Top | Mount | 1 | - | - | - | - | - | - |  | £0.000
 | M-13 | M2x16 Bolt | Bolt | 6 | - | M2x16 | - | - | - | - |  | £0.000
 | M-14 | M2x12 Bolt | Bolt | 6 | - | M2x12 | - | - | - | - |  | £0.000
 | M-15 | M2x8 Bolt | Bolt | 3 | - | M2x8 | - | - | - | - |  | £0.000
 | M-16 | M2 Nut | Nut | 12 | - | M2 | - | - | - | - |  | £0.000
 | M-17 | M2 Washer | Washer | 4 | - | M2 | - | - | - |  |  | £0.000
 | M-18 | M2 Threaded Inserts | Threaded Inserts | 2 | - | M2 | - |  |  | - |  | £0.000
 | M-19 | Servo Screw | Screw | 1 | - |  |  |  |  |  |  | £0.000 | Only Phillips head
 | Total |  |  |  |  |  |  |  |  |  |  | £27.993
Extras
 | E-01 | Base RC Car | Remote Controlled Car | 1 | - | - | Raster Toys | - | Argos | - | £12.000 | £12.000 |  | https://www.argos.co.uk/product/7655915?clickSR=slp:term:rc%20car:3:39:1
 | E-02 | MSP-EXP430G2ET Dev Board | Development Board | 1 | - | - | Texas Instruments | MSP-EXP430G2ET | DigiKey | 296-50264-ND | £9.510 | £9.510 |  | https://www.digikey.co.uk/en/products/detail/texas-instruments/MSP-EXP430G2ET/9608004?gad_source=1

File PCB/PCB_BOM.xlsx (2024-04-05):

Component | Value | Number | Link
MSP430 |  | ` | https://www.mouser.co.uk/ProductDetail/Texas-Instruments/MSP430G2553IN20?qs=cBe3DO7yhR7KujMhn3Ev6Q%3D%3D
IC Socket | 20 pin |  | https://www.mouser.co.uk/ProductDetail/TE-Connectivity/1-2199298-6?qs=fK8dlpkaUMvuMXpJTs4GlA%3D%3D
JST 2 way | 2 way |  | https://uk.farnell.com/jst-japan-solderless-terminals/b2b-ph-k-s-lf-sn/header-top-entry-2way-2mm/dp/9491856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
JST 3 way | 3 way |  | https://uk.farnell.com/jst-japan-solderless-terminals/b3b-xh-a-lf-sn/header-vertical-3way/dp/1516277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
JST 4 way | 4 way |  | https://uk.farnell.com/jst-japan-solderless-terminals/b4b-xh-a-lf-sn/header-vertical-4way/dp/1516278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
Cap | 0.1uF |  | https://www.mouser.co.uk/ProductDetail/YAGEO/CC0805KPX7R9BB104?qs=vTakOoo5QyLPWGiom%252Bf2Ug%3D%3D
Cap | 1 uF |  | https://www.mouser.co.uk/ProductDetail/Samsung-Electro-Mechanics/CL21B105KPFNNNE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
Cap | 10 uF |  | https://www.mouser.co.uk/ProductDetail/Samsung-Electro-Mechanics/CL21A106KQFNNNG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
resistors |  |  | https://www.mouser.co.uk/ProductDetail/Panasonic/ERJ-PB6B3002V
6 pin motor driver header |  |  | https://www.mouser.co.uk/ProductDetail/Wurth-Elektronik/61300611821?qs=iLbezkQI%252BsgS21jF2eozhA%3D%3D
3pin header |  |  | https://www.mouser.co.uk/ProductDetail/Preci-dip/801-87-003-10-001101?qs=FtMuP6KVi2T66jAxB5rZkg%3D%3D
v regulator |  |  | https://www.mouser.co.uk/ProductDetail/Texas-Instruments/TLV1117LV33DCYR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

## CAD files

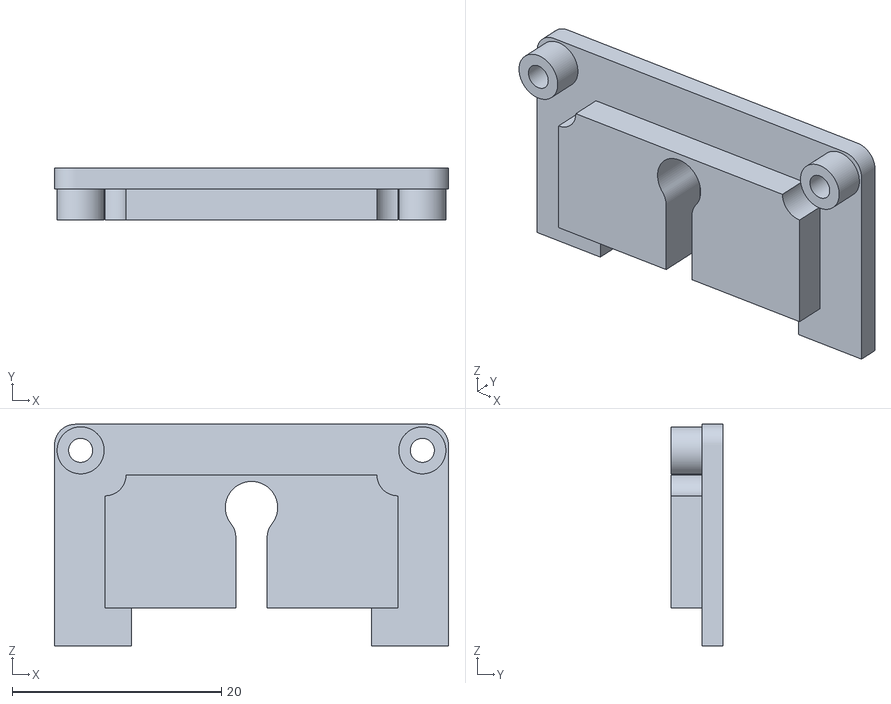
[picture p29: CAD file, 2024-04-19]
CAD/stls/7_ServoFullMountInsert_left.stl
37.7 x 5.00 x 21.2

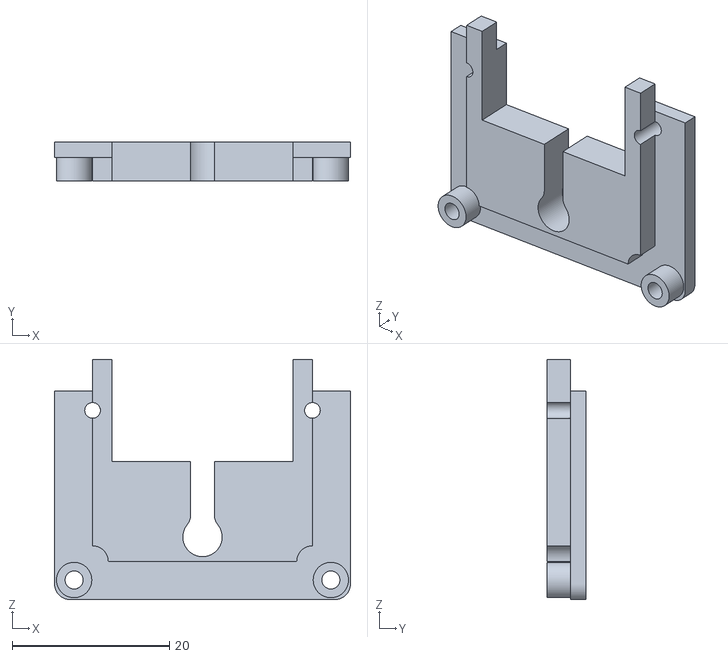
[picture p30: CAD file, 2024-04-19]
CAD/stls/8_ServoFullMountInsert_right.stl
37.7 x 5.00 x 30.6

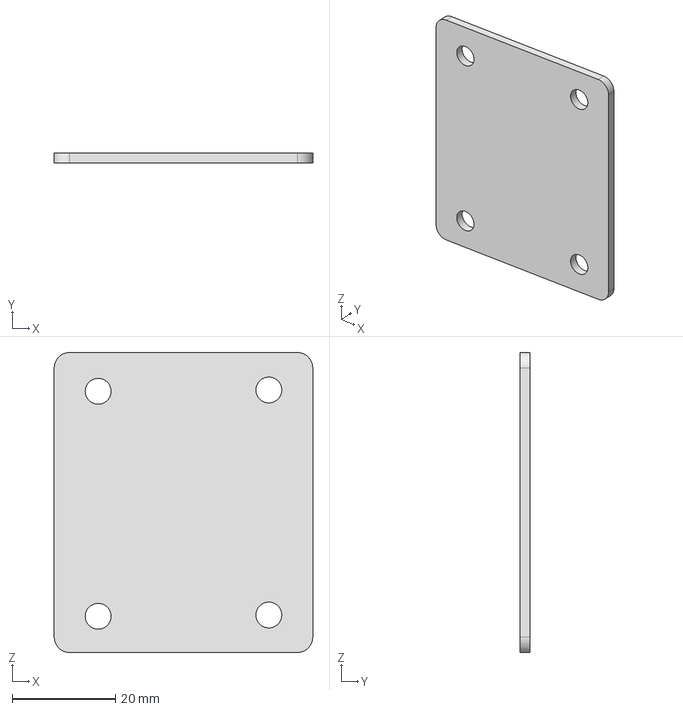
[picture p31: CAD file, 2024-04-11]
CAD/Components/PCB_design.stp
50.0 x 2.00 x 58.0 mm

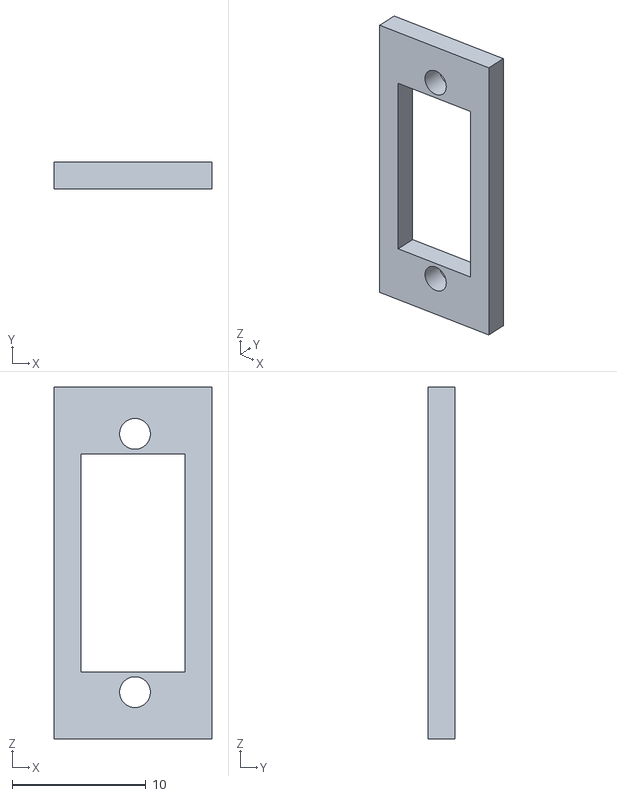
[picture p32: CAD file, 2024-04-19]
CAD/ControlPanelTests/SwitchTest.stl
11.8 x 2.00 x 26.3

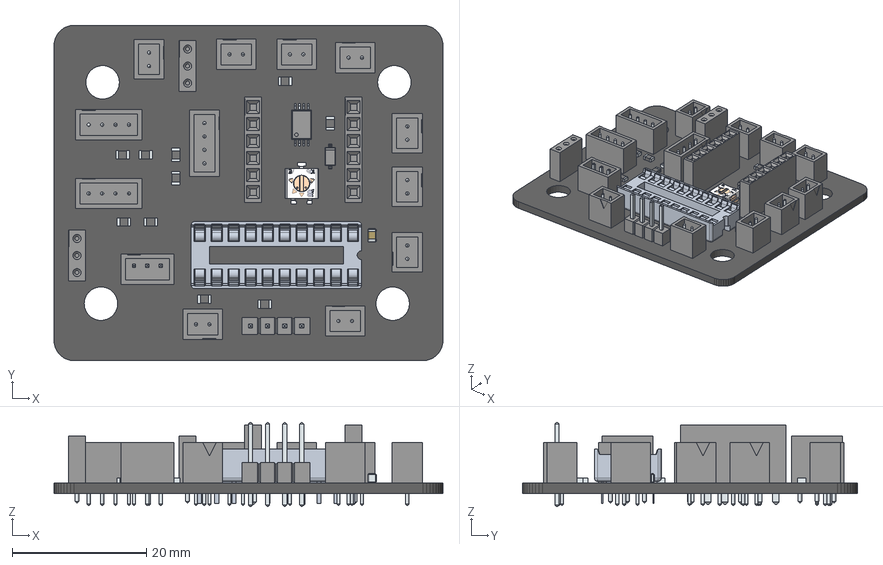
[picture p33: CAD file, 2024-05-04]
CAD/PCB/EE579_Skittles_pcb.step
58.0 x 50.0 x 12.6 mm
PinsArrayLR
FilletPinL
FilletPinR
term1 x 10
term2 x 10
LeadsArray x 18

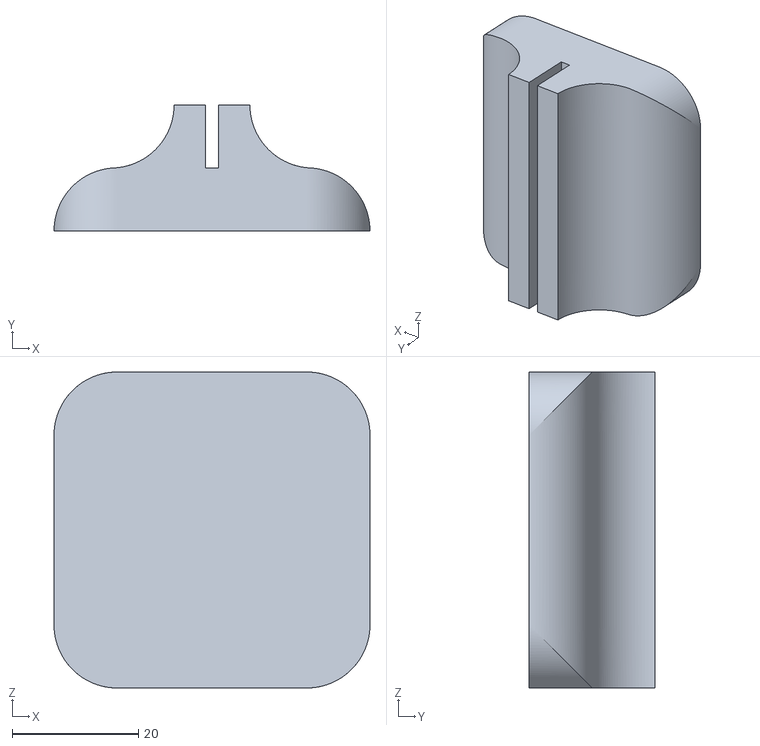
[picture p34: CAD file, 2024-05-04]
CAD/stls/CalibrationWallMounts.stl
50.0 x 20.0 x 50.0

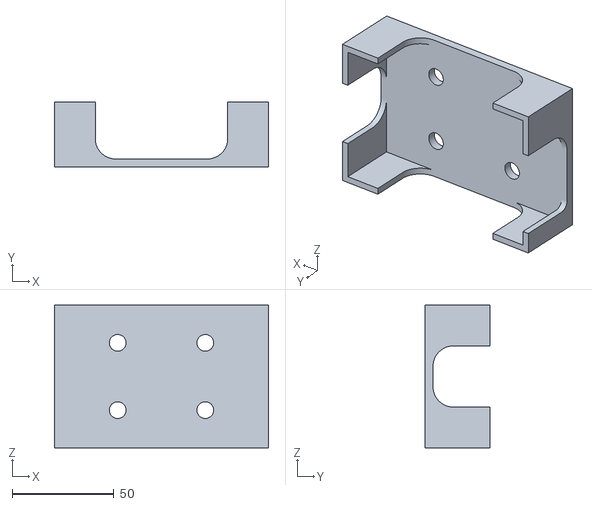
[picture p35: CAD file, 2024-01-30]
CAD/TestingPlatform/stls/TestingPlatform_base01.stl
105.0 x 32.0 x 70.0

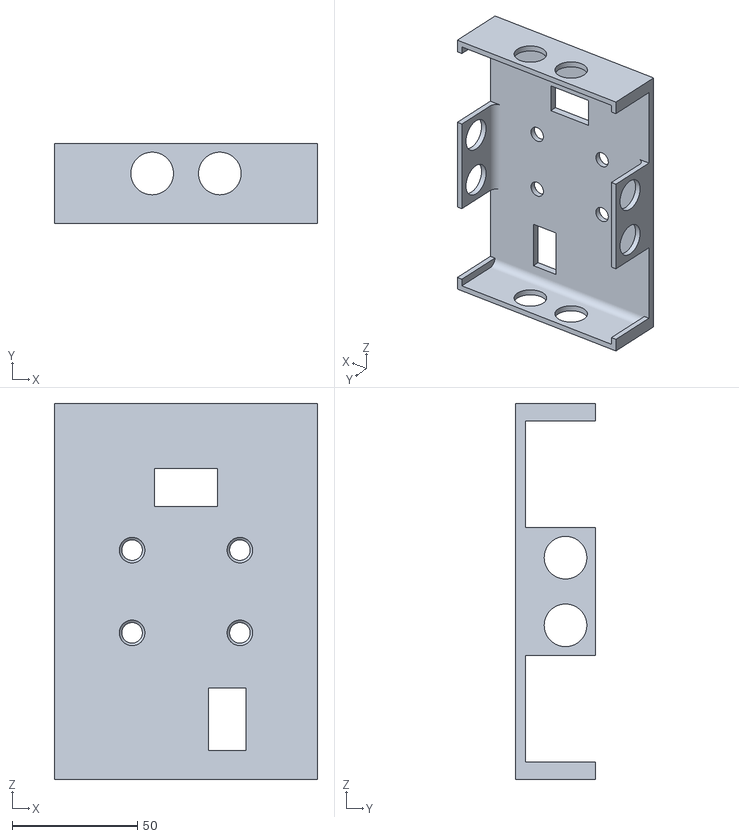
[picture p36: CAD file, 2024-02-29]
CAD/TestingPlatform02/TestingPlatform_base02.stl
105.0 x 32.0 x 150.0

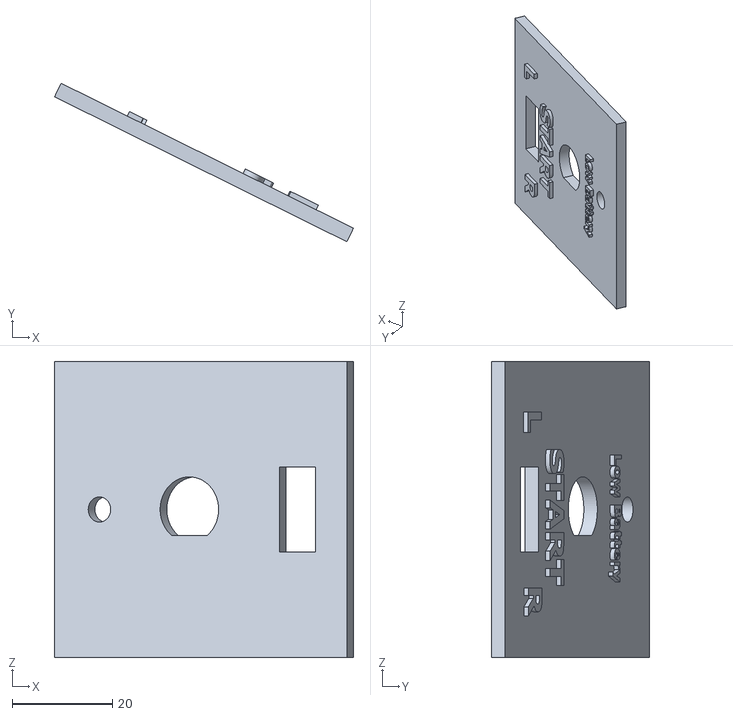
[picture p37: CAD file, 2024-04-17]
CAD/ControlPanelTests/ControlPanel_Top.stl
59.6 x 31.6 x 59.0

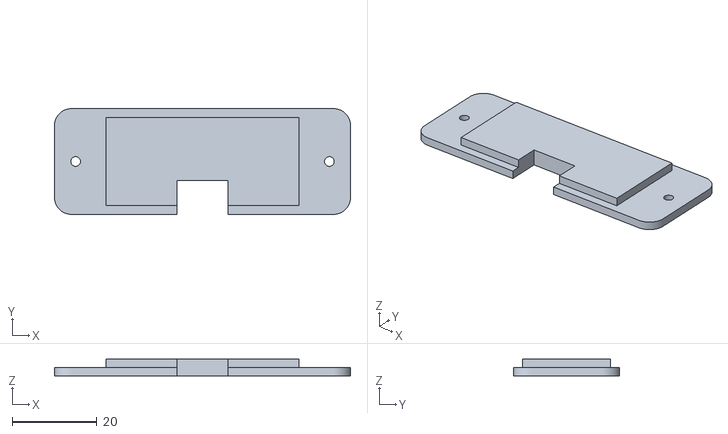
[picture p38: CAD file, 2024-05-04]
CAD/stls/4_UltrasonicSensorMount_backplate03.stl
70.0 x 25.0 x 4.00

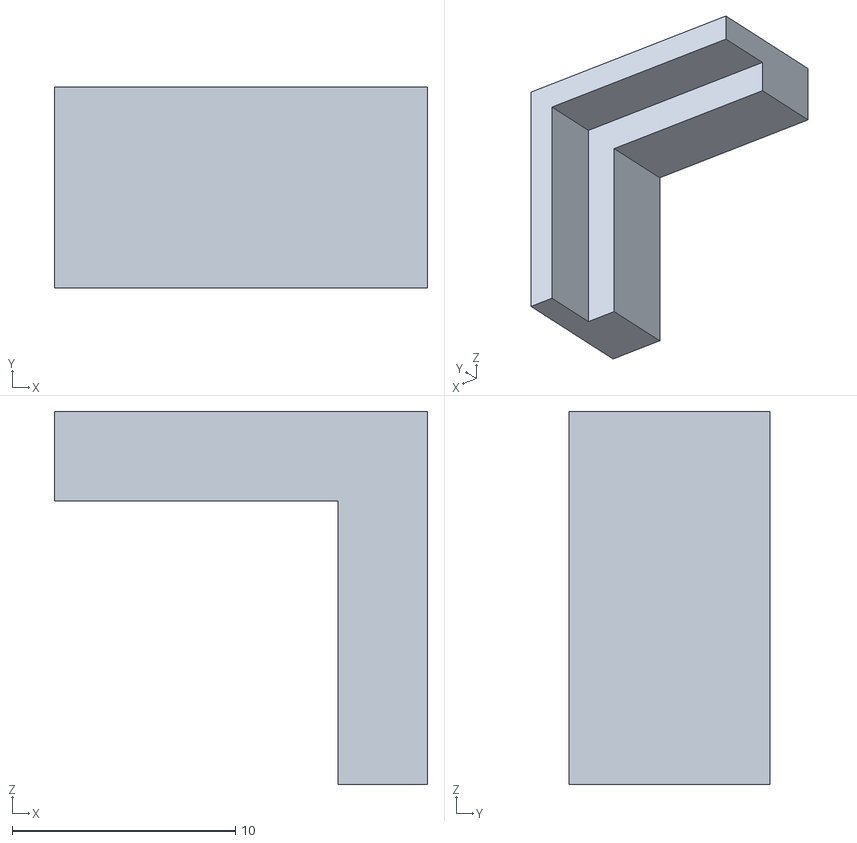
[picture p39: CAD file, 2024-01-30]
CAD/TestingPlatform/stls/TestingPlatform_stackFeet01.stl
16.7 x 9.00 x 16.7

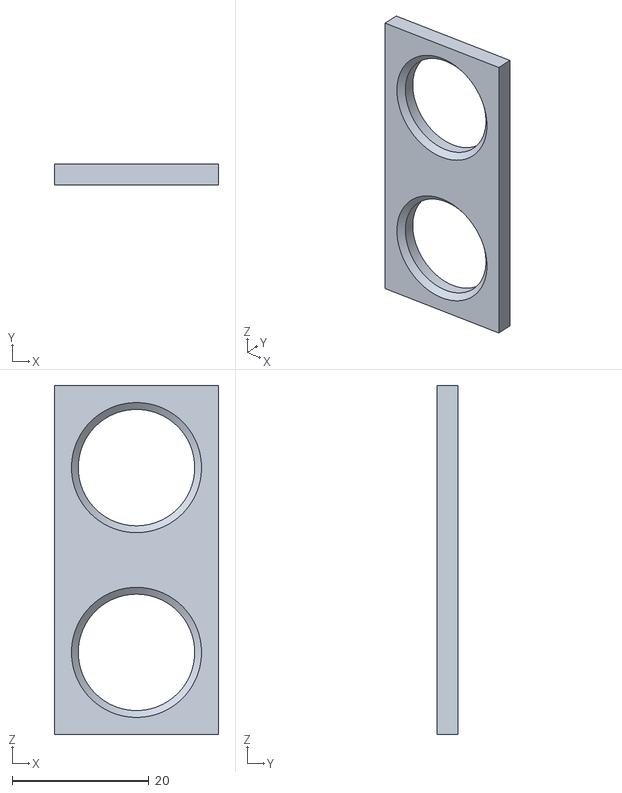
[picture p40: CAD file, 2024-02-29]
CAD/TestingPlatform02/UltrasonicMountTest01.stl
24.0 x 3.00 x 51.0

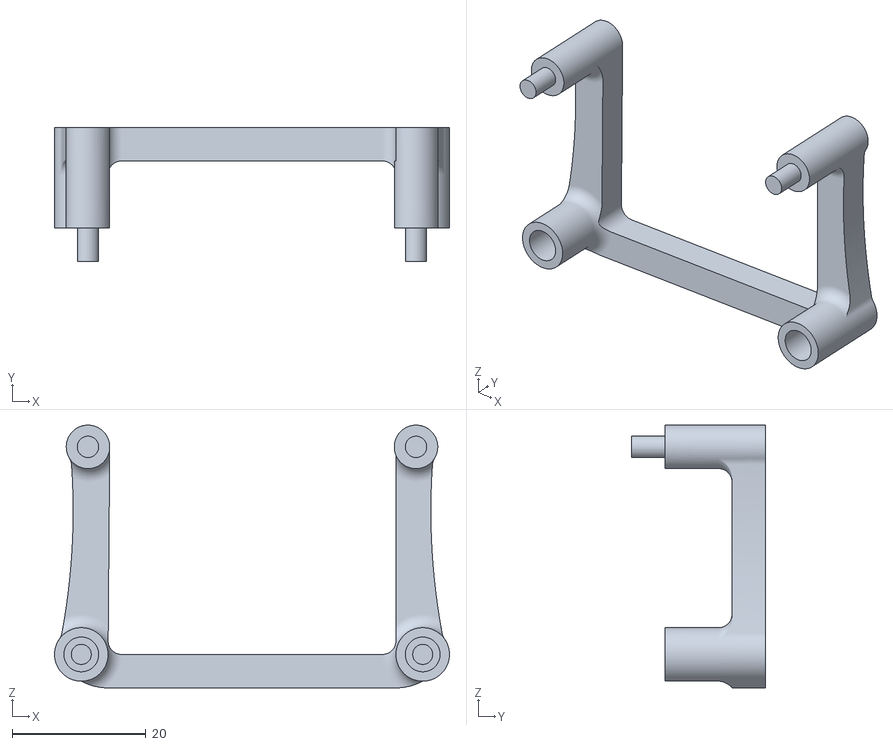
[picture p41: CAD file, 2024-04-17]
CAD/ControlPanelTests/ControlPanel_Top01.stl
59.0 x 20.0 x 39.2

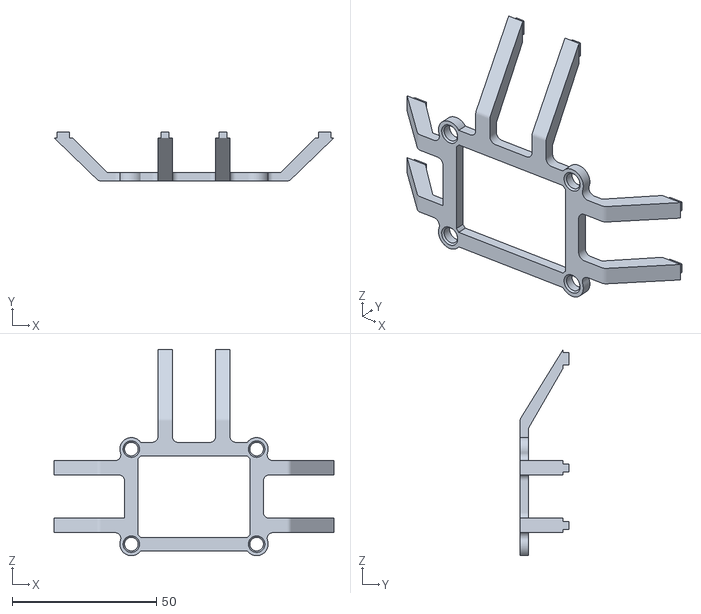
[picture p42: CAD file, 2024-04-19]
CAD/stls/2_Top_Mount.stl
97.2 x 17.0 x 71.6

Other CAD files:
PCB/PCB_design.stl
CAD/Components/EE579_Skittles_pcb.step
CAD/TestingPlatform/stls/TestingPlatform_legs01.stl
CAD/ControlPanelTests/text_test_cut_thru.stl
CAD/Assemblies/ControlPanel/ControlPanel.iam
CAD/Assemblies/ControlPanel/ControlPanel_assembly_exploded.idw
CAD/Assemblies/ControlPanel/ControlPanel_assembly_exploded.ipn
CAD/Assemblies/ControlPanel/OldVersions/ControlPanel.0003.iam
CAD/Assemblies/ControlPanel/OldVersions/ControlPanel_assembly_exploded.0004.idw
CAD/Assemblies/ControlPanel/OldVersions/ControlPanel_assembly_exploded.0006.ipn
CAD/Assemblies/Main/ControlPanel/MainAssembly_ControlPanel.idw
CAD/Assemblies/Main/ControlPanel/MainAssembly_ControlPanel.ipn
CAD/Assemblies/Main/MainAssembly.iam
CAD/Assemblies/Main/OldVersions/MainAssembly.0017.iam
CAD/Assemblies/Main/OldVersions/MainAssembly_ControlPanel.0001.idw
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

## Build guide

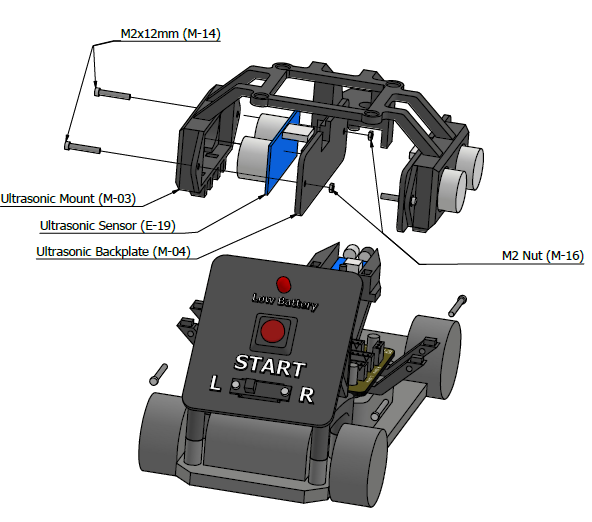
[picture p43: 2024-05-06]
CAD/Assemblies/Main/SideSonar/MainAssembly_SideSonar.png

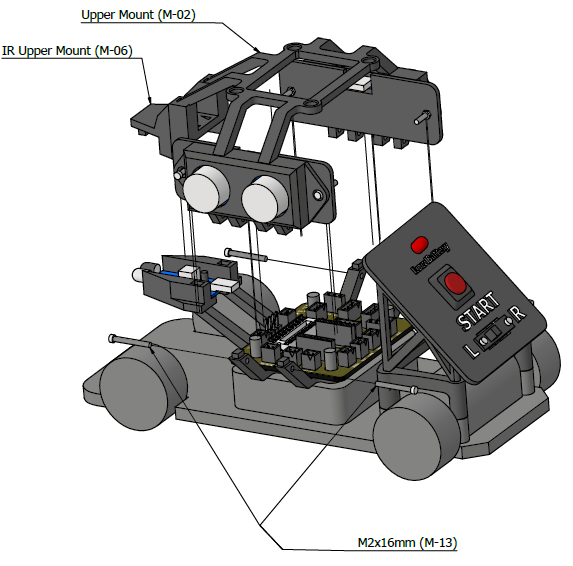
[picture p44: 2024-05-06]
CAD/Assemblies/Main/TopStructure/MainAssembly_TopStructure.png

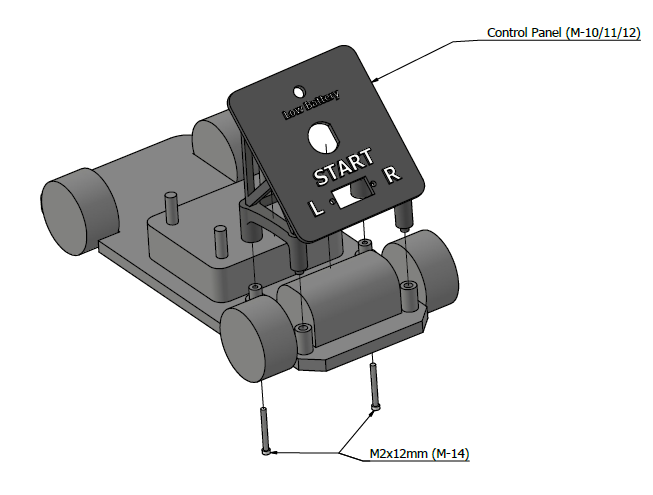
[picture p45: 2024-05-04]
CAD/Assemblies/ControlPanel/ControlPanel_assembly_exploded.png

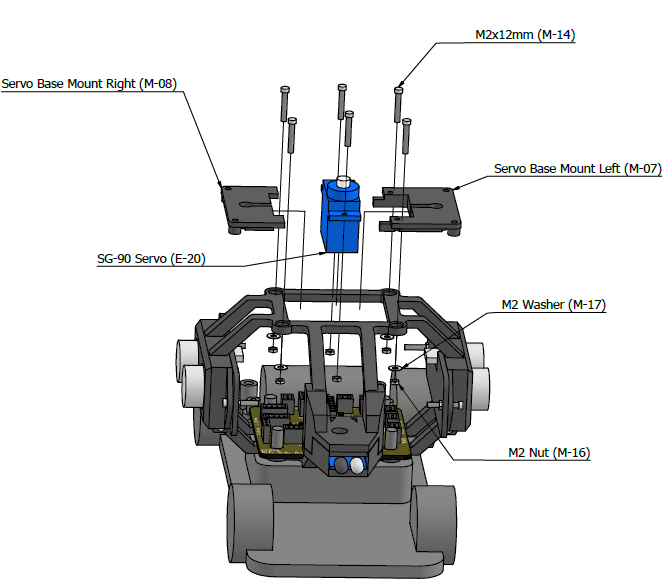
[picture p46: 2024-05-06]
CAD/Assemblies/Main/ServoStructure/MainAssembly_ServoStructure.png

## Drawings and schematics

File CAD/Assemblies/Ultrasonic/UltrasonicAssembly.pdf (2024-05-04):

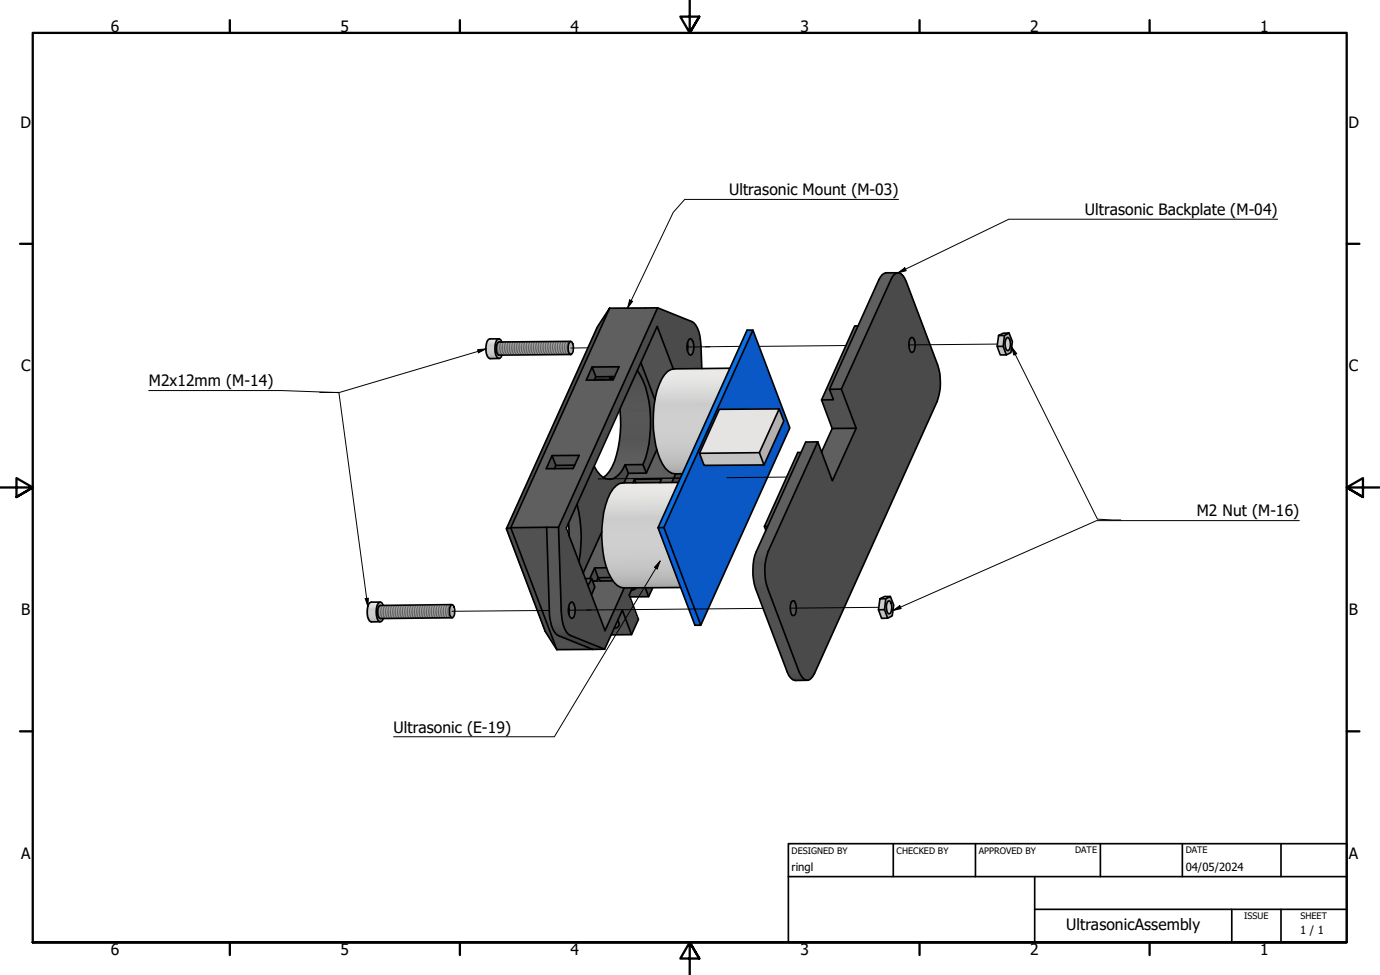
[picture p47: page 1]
DESIGNED BY; CHECKED BY; APPROVED BY; DATE; Ultrasonic (E-19); M2 Nut (M-16); Ultrasonic Mount (M-03); Ultrasonic Backplate (M-04)

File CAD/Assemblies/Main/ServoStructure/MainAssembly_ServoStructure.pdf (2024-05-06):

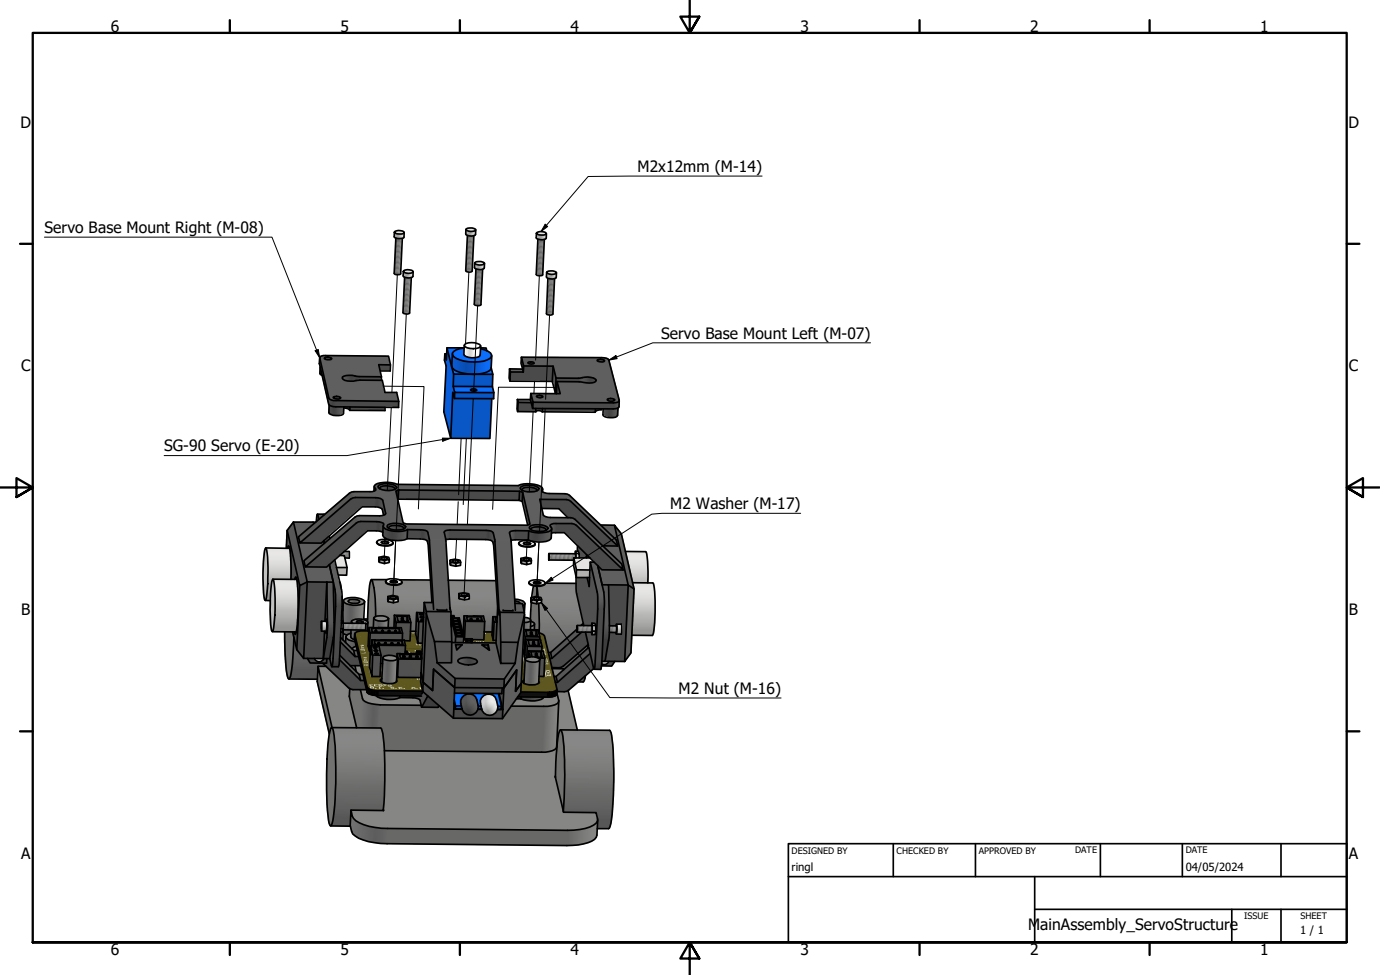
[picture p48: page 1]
DESIGNED BY; CHECKED BY; APPROVED BY; DATE; SG-90 Servo (E-20); M2 Nut (M-16); M2 Washer (M-17)

Servo Base Mount Right (M-08)

Servo Base Mount Left (M-07)

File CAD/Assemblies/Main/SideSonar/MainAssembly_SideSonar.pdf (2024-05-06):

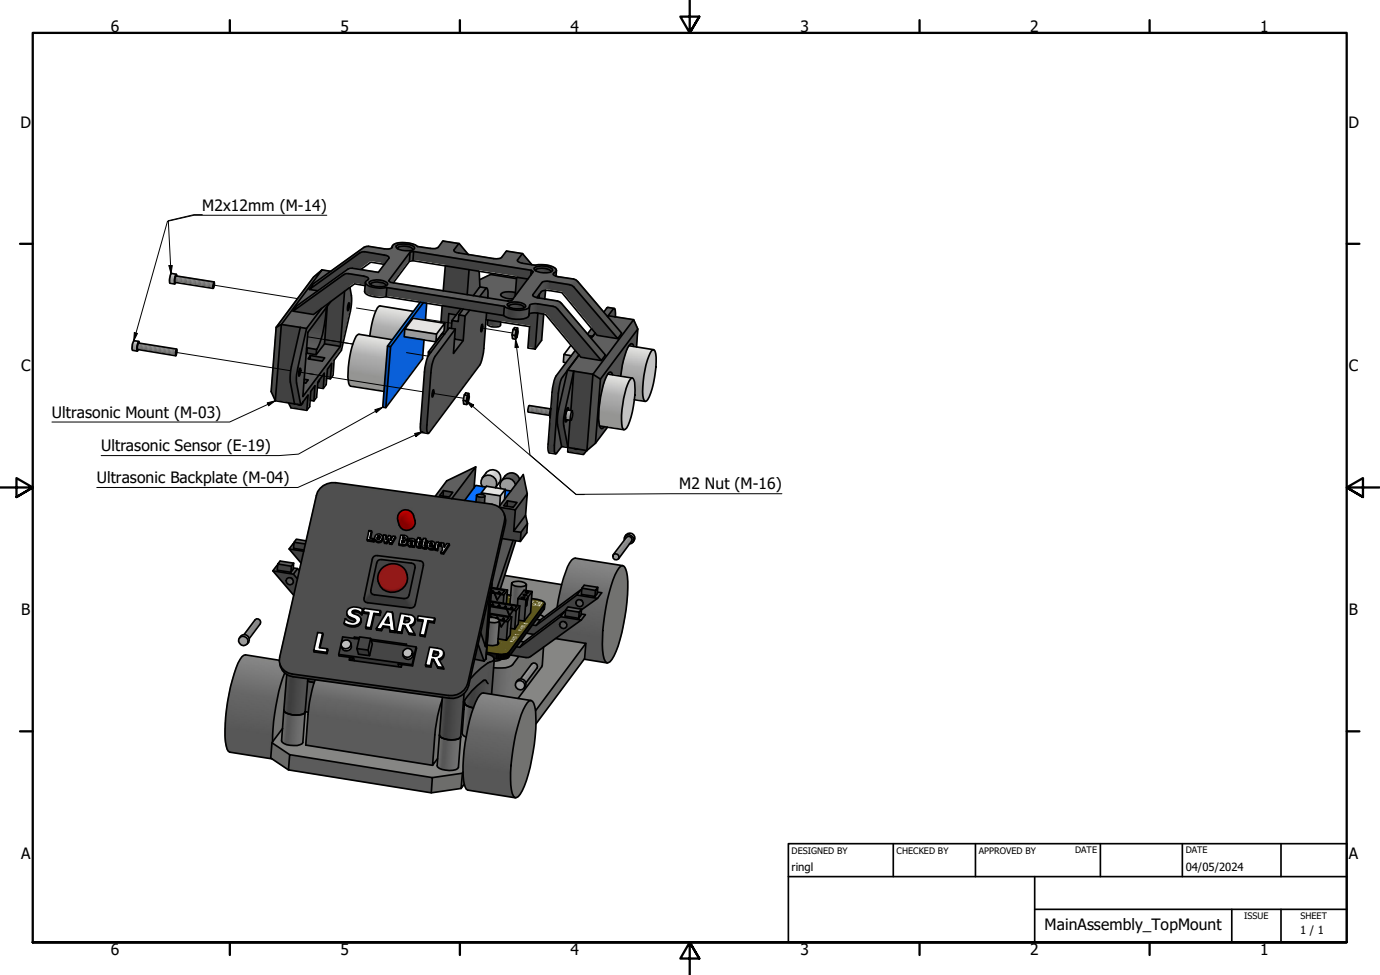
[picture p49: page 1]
DESIGNED BY; CHECKED BY; APPROVED BY; DATE; Ultrasonic Sensor (E-19); Ultrasonic Backplate (M-04); M2 Nut (M-16); Ultrasonic Mount (M-03)

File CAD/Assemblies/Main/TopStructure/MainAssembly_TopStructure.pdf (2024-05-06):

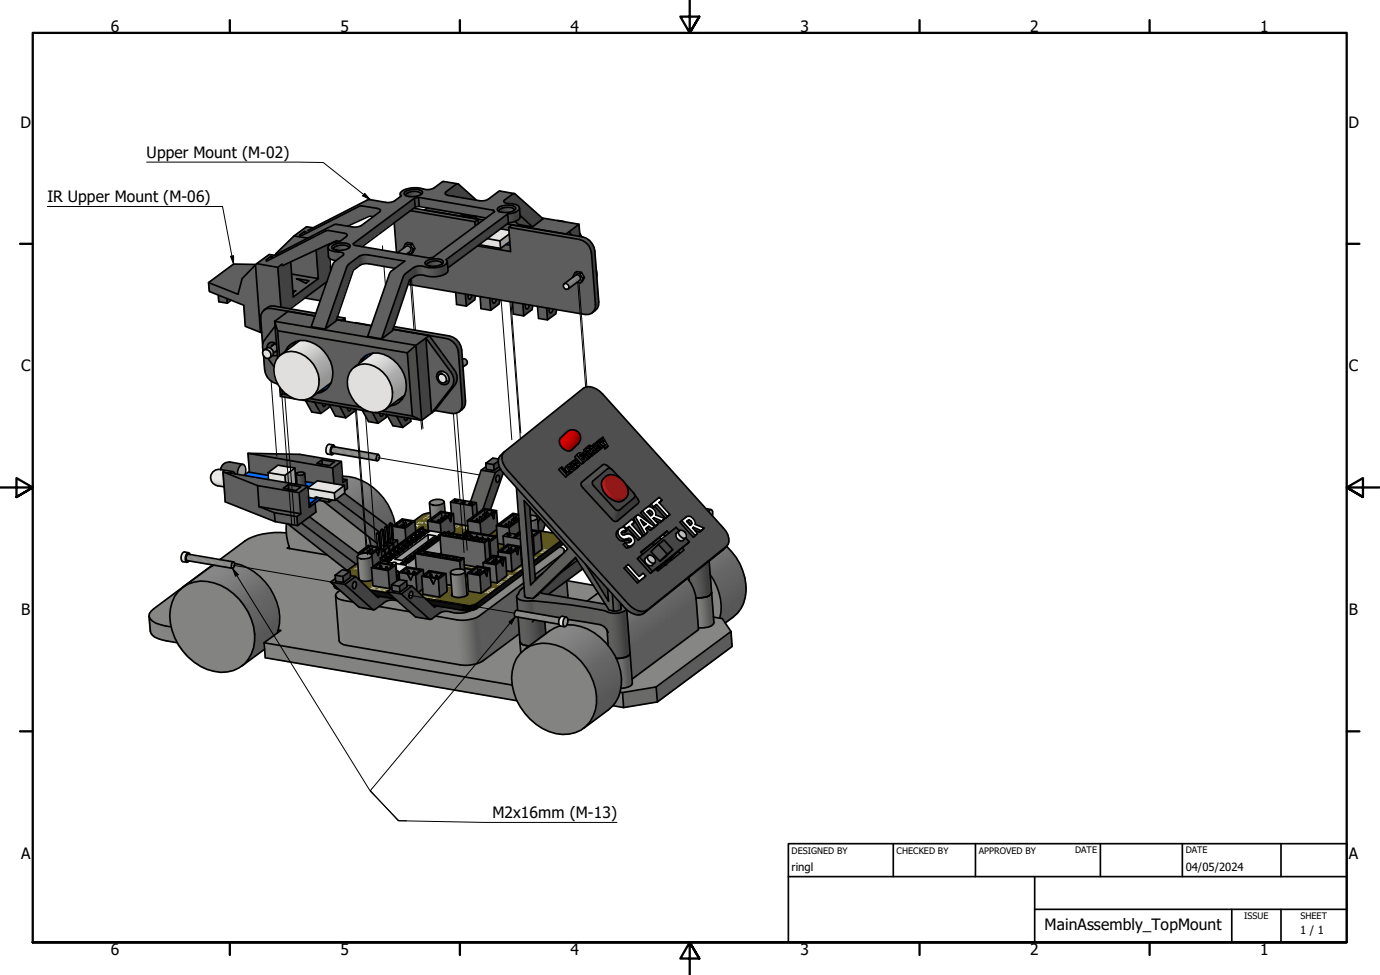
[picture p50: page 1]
DESIGNED BY; CHECKED BY; APPROVED BY; DATE; Upper Mount (M-02)

IR Upper Mount (M-06)

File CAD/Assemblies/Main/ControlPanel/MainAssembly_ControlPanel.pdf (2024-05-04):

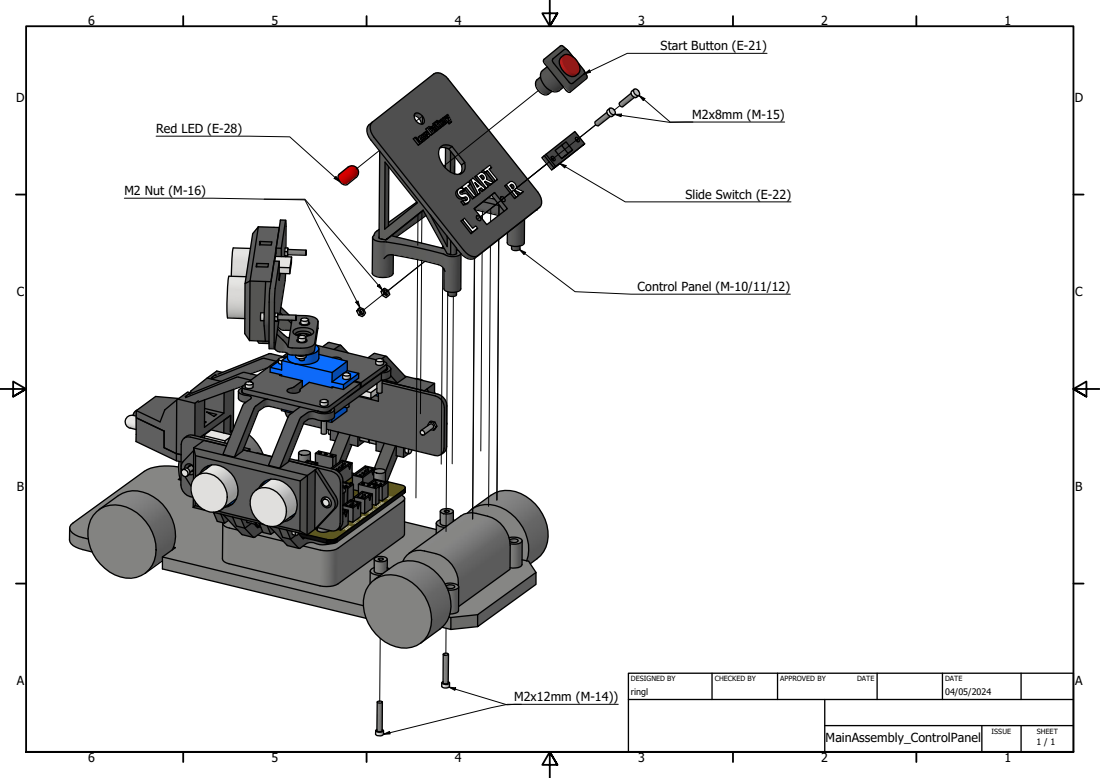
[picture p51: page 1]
DESIGNED BY; CHECKED BY; APPROVED BY; DATE; Start Button (E-21); Red LED (E-28); Slide Switch (E-22); 2 Nut (M-16); Control Panel (M-10/11/12)

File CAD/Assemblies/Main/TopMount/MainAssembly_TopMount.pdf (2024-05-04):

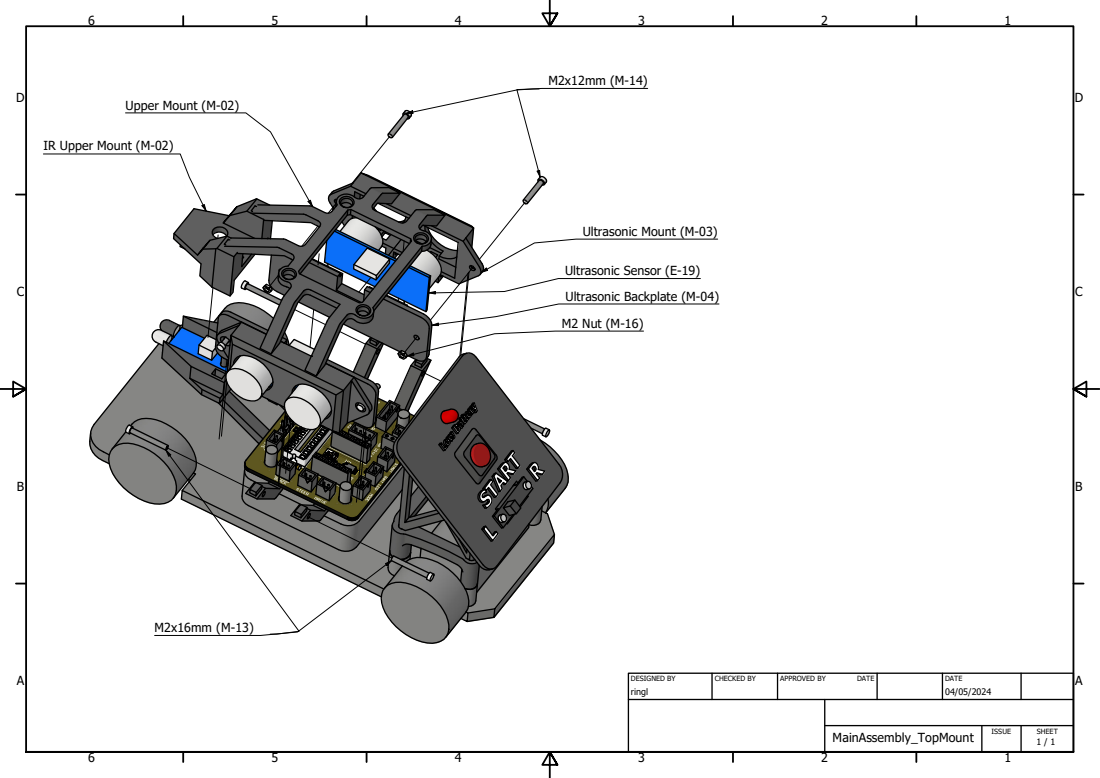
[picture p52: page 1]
DESIGNED BY; CHECKED BY; APPROVED BY; DATE; Upper Mount (M-02); Ultrasonic Mount (M-03); Ultrasonic Sensor (E-19); Ultrasonic Backplate (M-04); M2 Nut (M-16)

IR Upper Mount (M-02)

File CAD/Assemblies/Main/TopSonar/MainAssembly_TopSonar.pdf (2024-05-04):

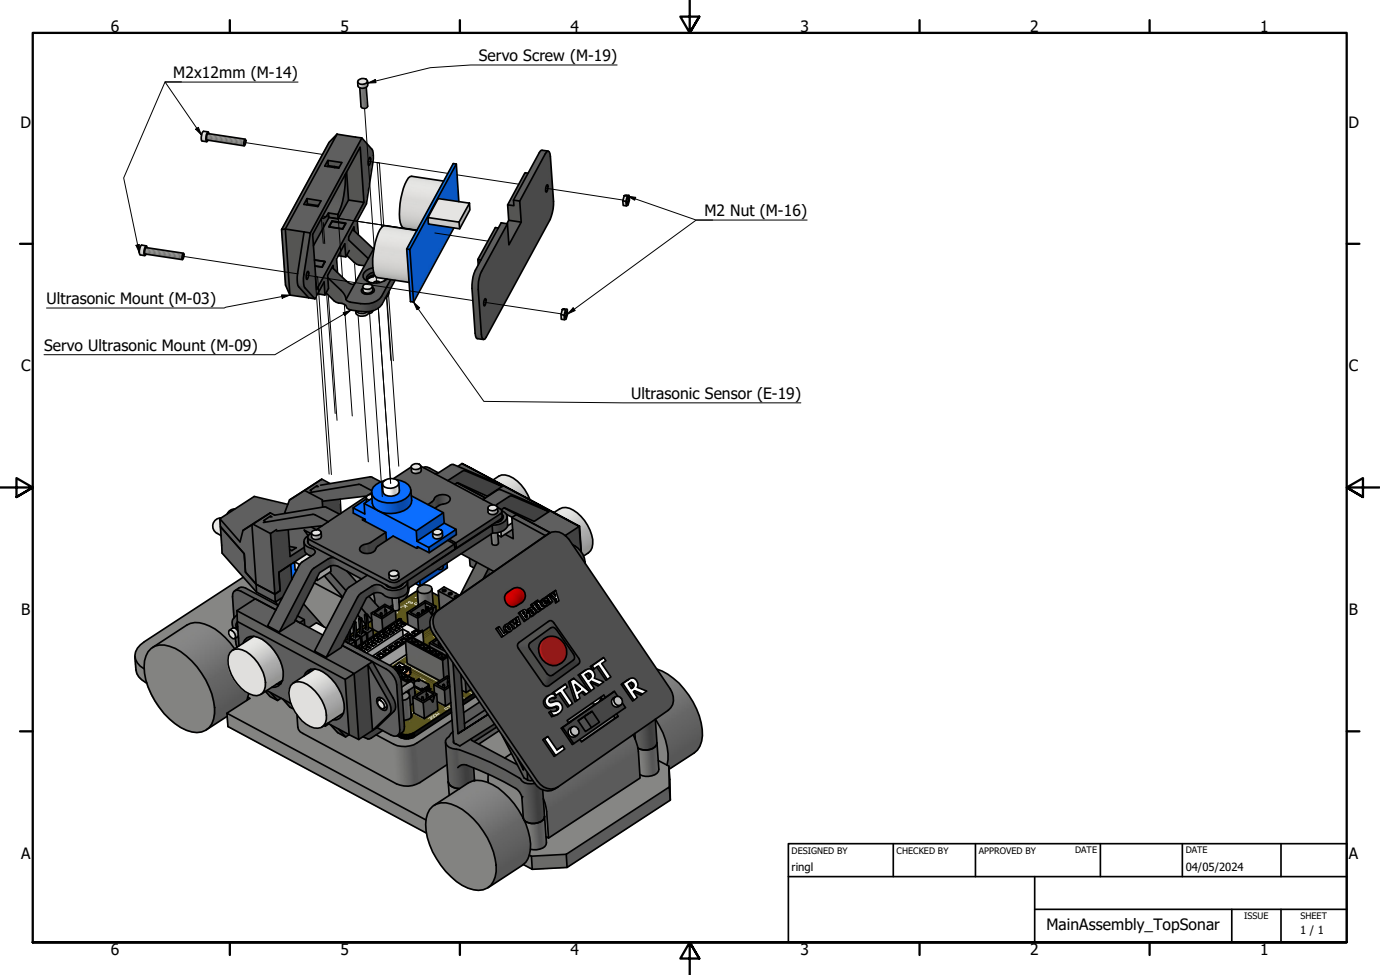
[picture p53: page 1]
DESIGNED BY; CHECKED BY; APPROVED BY; DATE; Servo Screw (M-19); M2 Nut (M-16); Ultrasonic Sensor (E-19); Ultrasonic Mount (M-03)

Servo Ultrasonic Mount (M-09)

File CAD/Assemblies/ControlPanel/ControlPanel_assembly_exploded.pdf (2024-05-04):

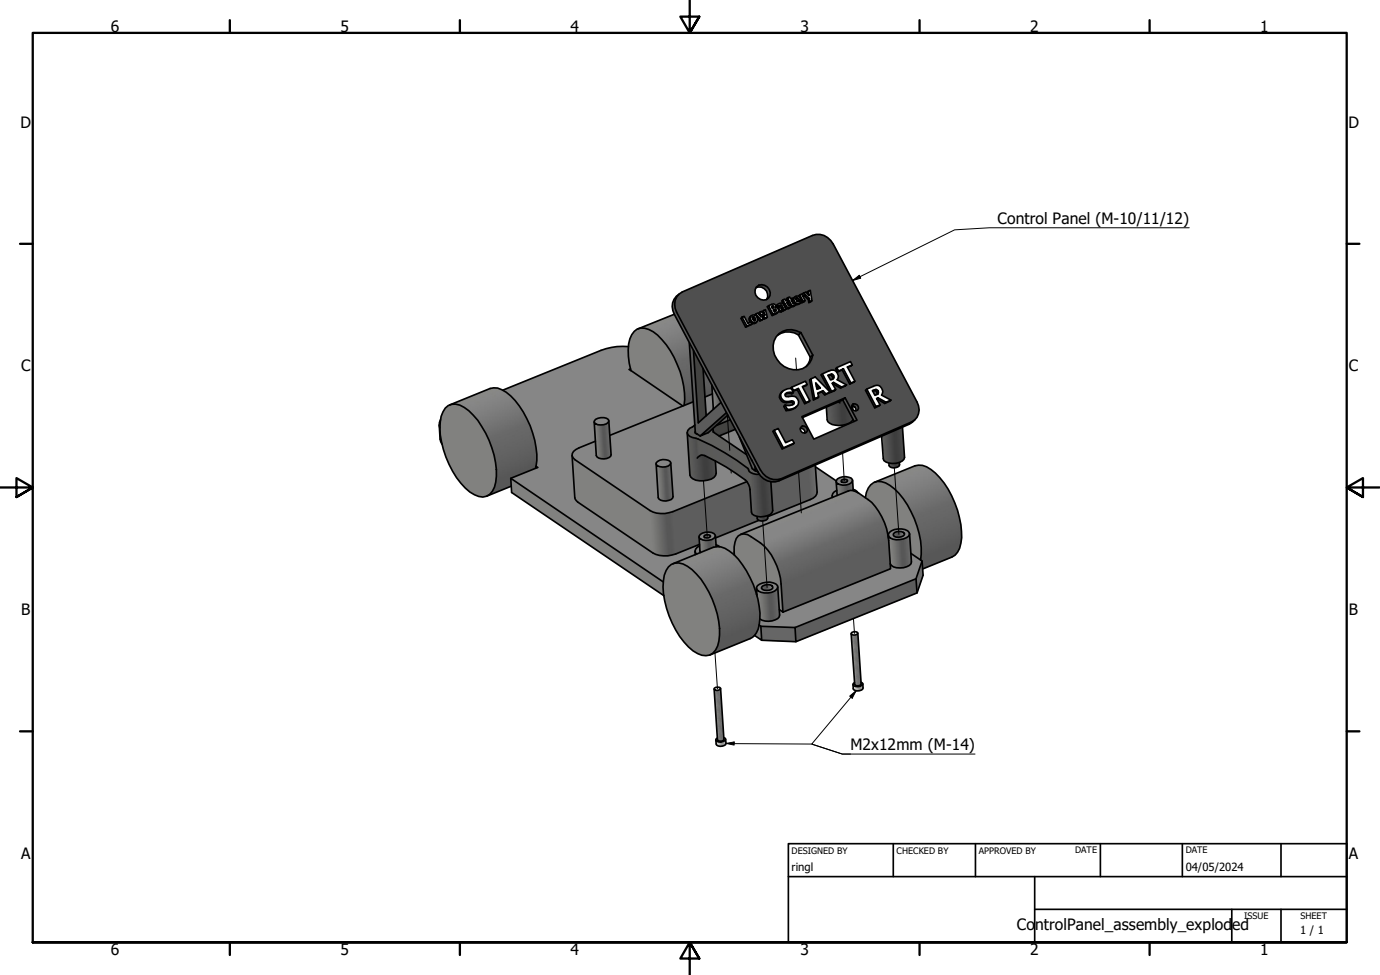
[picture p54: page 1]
DESIGNED BY; CHECKED BY; APPROVED BY; DATE; Control Panel (M-10/11/12)

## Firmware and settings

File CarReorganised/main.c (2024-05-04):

/*
Filename    : CarReorganised/main.c
Author      : Samuel Kliskey
Project     : EE579 Skittles Knocking Over Project
Date        : 31/3/24
Description : Main script to control functions of the autonomous vehicle
              to as quickly as possible knock over black skittles and avoid
              white skittles.
--------------------------------------------------------------------------------
Change History
--------------------------------------------------------------------------------
31-MAR-2024 SARK created to restructure AutonomousCar project
01-APR-2024 SARK continued to restructure to make readable
05-APR-2024 SARK added multiple ultrasonic sensors
06-APR-2024 SARK fine tuned car to follow wall and stop beside can
07-APR-2024 SARK added SONAR scan to lock on to car
08-APR-2024 SARK fixed bug with ultrasonic readings and timer overflows
08-APR-2024 SARK added code for car to approach can
09-APR-2024 SARK added right ultrasonic code
09-APR-2024 RI added AL's IR sensor functionality
10-APR-2024 SARK debugged to allow car to nudge into a can
11-APR-2024 SARK got car to knock over a can & started looking into colour sensing
12-APR-2024 SARK got colour sensing to work and working on realigning to wall with SONAR
13-APR-2024 SARK working on retracing steps to realign to wall as SONAR unsuccessful
15-APR-2024 SARK implemented realigning to wall with side ultrasonic
16-APR-2024 SARK fixed changing wall position bug by aligning to wall with changes in
            reading instead of absolute distance to wall
22-APR-2024 SARK implemented left and right ultrasonic sensors as well as allowing
            "wall to align to" to be controllable by switch
01-MAY-2024 SARK trying one last realignment fix & commenting all of code
03-MAY-2023 SARK optimised code for demo on demo day. Car won the competition!
--------------------------------------------------------------------------------
*/

//==============================================================================
// External Files
//------------------------------------------------------------------------------
//External
#include <msp430.h>

//Local
#include "DCMotor.h"
#include "Servo.h"
#include "Ultrasonic.h"
#include "UserInterface.h"
#include "Infrared.h"

//==============================================================================
// User-Defined Types
//------------------------------------------------------------------------------
//Define time structure
struct Time {
    int sec;
    int ms;
};

//Contains flags from various hardware sources to inform changes or readings
struct flags {
    //When button is pressed
    char button;

    //When button debounce has finished
    char debounce;

    //When the nature of the car changes
    char stateChange;

    //When schedule timer ticks
    char timerA0;

    //When motor needs to change state
    char motorDrive;
    char motorSteer;

    //To read ultrasonic when result available
    char ultraLeftRead;
	char ultraRightRead;
    char ultraSONARRead;
};

//Structure contains all timings that events occur on
struct Scheduler {
    //Time at which debouncing finishes
    struct Time debounce;

    //Time to start an ultrasonic reading
    struct Time ultraLeftStart;
	struct Time ultraRightStart;
	struct Time ultraSONARStart;

	struct Time ultraLeftStartBackup;
    struct Time ultraRightStartBackup;
    struct Time ultraSONARStartBackup;

    //Time at which car state should change
    struct Time stateChange;

    //Time at which motor PWM should change
    struct Time pwmMotorDrive;
    struct Time pwmMotorSteer;

    //Time to change movement
    struct Time movementChange;
	
	//Time to start searching for cans
	struct Time searchStart;
};

//==============================================================================
// Function Prototypes
//------------------------------------------------------------------------------
//Interrupt Service Routines
__interrupt void Port1_ISR(void);
__interrupt void Timer0_A0_ISR(void);
__interrupt void Timer0_A1_ISR(void);
__interrupt void Timer1_A0_ISR (void);
__interrupt void Timer1_A1_ISR (void);

//Hardware setup
void    setupTimerSchedule();
void    setupTimerSONAR();

//Main functionality of code
int     main(void);
void    checkFlags();
void	stateControl();
void    changingState();

//Scheduler functions
void    checkSchedule();
void    timeIncrement(struct Time *time, int sec, int ms);

//Sonar Functionality
void    canLock();
void    SONAR();

//Navigation Functionality
void    alignToWall();
void    circumnavigate();
void    updateCarHeading(unsigned char direction, unsigned char angle, unsigned int speed);

//Other functionality
void    findDistanceAverage(unsigned char start, unsigned char end, unsigned int *values);

//==============================================================================
// MACROs
//------------------------------------------------------------------------------
//Available clock information
#define SMCK_FREQ      1000000
#define ACLK_FREQ      32768

// Important Ultrasonic Info
#define SOUND_SPEED 343
#define CLOCK_USED_ULTRASONIC   SMCK_FREQ
#define dist2pulse(d)           ((CLOCK_USED_ULTRASONIC/100)*d*2/SOUND_SPEED)     // Converts a distance (cm) to ultrasonic sensor output pulse length

//Scheduler information
#define CLOCK_USED_SCHEDULER    SMCK_FREQ
#define SECOND_COUNT   			1000		//1000 ms = 1s
#define isTime(X) ((currentTime.sec == X.sec) && (currentTime.ms == X.ms))

//Car States
#define CAN_CALIBRATION 0
#define READY       	1
#define SEARCH      	2
#define CAN_ALIGN   	3
#define SONAR_SCAN  	4
#define CAN_APPROACH	5
#define COLOUR_DETECT 	6
#define REVERSE_CAN     7
#define CAN_HIT			8
#define CIRCUMNAVIGATE  9
#define WALL_REALIGN    10
#define STOP        	11

//Wall alignment
#define STRAIGHT    	0
#define AWAY        	1
#define CLOSE       	2
#define STRAIGHTEN  	3

//==============================================================================
// CHANGEABLE SETTINGS MACROs
//------------------------------------------------------------------------------
//Scheduler control
#define TIMER_INC_MS    2                   //Scheduler interrupts period (2 ms)

//Drive Speeds
#define MOTOR_PWM_PERIOD    100             //PWM period of motors.

//Wall readings control
#define WALL_READINGS   5                   //Number of wall readings remembered (MAKE 1+2^x)
#define AVERAGE_SHIFT   2					//log2(WALL_READINGS-1), used for computationally efficient find average
#define TIME_BEFORE_SEARCHING   6           //Time in seconds on start before searching
#define FIND_SPEED    35                    //Speed once in search time
#define SPRINT_SPEED  60                    //Sprint speed to get to search area

//SONAR Reading control
#define SONAR_READINGS   5					//Make equal to wall readings
#define MAX_FRONT_DETECT 2500               //Distance front can is detected in
#define ANOMALY_DISTANCE 500                //Distance drop off for start of anomaly in SONAR()

//SONAR SCANNING
#define NUMBER_OF_ANGLES_CHECKED    15      //Number of angles in SONAR sweep

//CAN ALIGN
#define INITIAL_CAN_ALIGN_SEC   0           //Time to re-adjust from initial detection and parallel
#define INITIAL_CAN_ALIGN_MS    900
#define SECONDARY_CAN_ALIGN_SEC 1           //Time to re-adjust after approached can but at a bad angle
#define SECONDARY_CAN_ALIGN_MS  100

//CAN APPROACH
#define FACE_CAN_ANGLE_TOLERANCE    100     //Directly facing tolerance (In servo PWM period ~15 degrees)
#define FACE_CAN_DIST_TOLERANCE     600     //Distance away tolerance (Ultrasonic pulse length ~6 cm)
#define CAN_APPROACH_SPEED          40      //Speed when approaching

//REVERSE TIME FOR RUN UP TO CAN
#define REVERSE_TIME   750                  //750 ms reverse

//HIT CAN
#define HIT_TIME   900                      //Time to drive into can for

//==============================================================================
// Global Variable Initialisation
//------------------------------------------------------------------------------
//Scheduling variables
struct Time currentTime     =   {0, 0};    //Running count of time
struct Scheduler Schedule   =   {0};       //Schedule when events should
struct flags flag           =   {0};       //Flag when something needed to be attended

//Hardware Variable Instantiation
//Indicator LED (Port 2)
struct IndicateLED LEDRed = {2, BIT5};
struct IndicateLED LEDBlue = {2, BIT6};
//Starting side switch
struct Switch sideSelect = {1, BIT1, 0};
//Button to control
struct Button startButton = {1, BIT3, 0};
//DC Motor info (Port 1)
struct MotorDC motorDrive = {0, BIT6, BIT7, {0, MOTOR_PWM_PERIOD, 0, 40, 1}};
struct MotorDC motorSteer = {0, BIT4, BIT5, {0, MOTOR_PWM_PERIOD, 0, MOTOR_PWM_PERIOD, 1}};
//Wall Ultrasonic info (Port 2)
struct Ultrasonic ultraLeft = {0, {0, 0}, 0, BIT0, BIT2, 2};
struct Ultrasonic ultraRight = {0, {0, 0}, 0, BIT0, BIT1, 2};
//SONAR Ultrasonic info (Port 1)
struct Ultrasonic ultraSONAR = {0, {0, 0}, 0, BIT0, BIT2, 1};
//Servo info (Port 2)
struct Servo servoSONAR = {BIT4, (PWM_SERVO_UPPER-PWM_SERVO_LOWER)/NUMBER_OF_ANGLES_CHECKED, 0};
// IR info (Port 2)
struct Infrared IR = {2, BIT3, 2};

//General Variables
unsigned int avgReading = 0;
unsigned int avgOldReading = 0;
unsigned int avgNewReading = 0;
unsigned int i = 0;
unsigned int j = 0;

//What car should be doing
char previousState  =   CAN_CALIBRATION;
char state          =   CAN_CALIBRATION;
char nextState      =   CAN_CALIBRATION;

//Calibrate Wall Variables
unsigned char fillBufferCount = 0;
unsigned char startSide = STRAIGHT;
unsigned int searchSpeeds = 50;

//Wall alignment & search info
char turnState = STRAIGHT;				//Wall alignment turning instruction
unsigned int  wallDistancesLeft[WALL_READINGS] = {[0 ... WALL_READINGS-1] = 0};	//Distance readings to left wall
unsigned int  wallDistancesRight[WALL_READINGS] = {[0 ... WALL_READINGS-1] = 0};	//Distance readings to left wall
unsigned char canPosition = STRAIGHT;
unsigned char search = 0;
unsigned int SONARDistances[SONAR_READINGS] = {[0 ... SONAR_READINGS-1] = 2000};
unsigned int furthestCanLeft = 0;
unsigned int furthestCanRight = 0;
unsigned char firstCanFound = 0;

//Can alignment
unsigned int timeToCanAlignSec = 0;
unsigned int timeToCanAlignMs = 0;

//SONAR Scan Variables
unsigned char readingsOnAngle = 0;
unsigned char anglesChecked = 0;
unsigned char anomalyPositions[NUMBER_OF_ANGLES_CHECKED] = {0};
unsigned char anomalyNumber = 0;
unsigned char canAnomaly = 0;
unsigned char anomalyStart[NUMBER_OF_ANGLES_CHECKED] = {[0 ... NUMBER_OF_ANGLES_CHECKED-1] = 0};;
unsigned char anomalyEnd[NUMBER_OF_ANGLES_CHECKED] = {[0 ... NUMBER_OF_ANGLES_CHECKED-1] = 0};;
unsigned int SONARAtEachAngle[NUMBER_OF_ANGLES_CHECKED] = {[0 ... NUMBER_OF_ANGLES_CHECKED-1] = 0};
unsigned int newAngle;

//Approaching can variables
unsigned char lostCan = 0;
unsigned int  lostCount = 0;
unsigned int  avgAnomalyDistance = 64000;
unsigned int  expectedCanDistance = 64000;
unsigned int  avgNewAnomalyDistance = 64000;

//Circumnavigate
unsigned char movement = 0;
unsigned char furtherWall = STRAIGHT;

//Wall realignment
unsigned int straightTime = 0;

//Flags for after event flags are dealt with and then results are used in stateControl()
char buttonPressed = 0;
char ultraReadLeft = 0;
char ultraReadRight = 0;
char ultraSONARRead = 0;


//==============================================================================
// Functions
//------------------------------------------------------------------------------
//Flag that button has been pressed
#pragma vector=PORT1_VECTOR
__interrupt void Port1_ISR(void)
{
    //Flag that button has been triggered
    flag.button = 1;
    __low_power_mode_off_on_exit();
    P1IFG &= ~BIT3;
    return;
}

//Flag that time has passed, update current time
#pragma vector=TIMER0_A0_VECTOR
__interrupt void Timer0_A0_ISR(void)
{
        //Increment time
        currentTime.ms += TIMER_INC_MS;
        if(currentTime.ms >= SECOND_COUNT)
        {
            currentTime.ms -= SECOND_COUNT;
            if(++currentTime.sec == 300) currentTime.sec = 0;
        }
        flag.timerA0 = 1;

        //If wrap occurs during SONAR ultrasonic pulse increment a wrap
        if (ultraSONAR.timeNumber != 0)
        {
            ultraSONAR.time[1] += TA0CCR0;
        }

        __low_power_mode_off_on_exit();
        TA0CCTL0 &= ~CCIFG;
}

//Triggered by ultrasonic return pulse
#pragma vector=TIMER0_A1_VECTOR
__interrupt void Timer0_A1_ISR(void)
{
    switch(TA0IV)
    {
        //On SONAR as interrupt source
        case TA0IV_TACCR1:
            ultraSONAR.time[ultraSONAR.timeNumber] += TA0CCR1;  //Set value of interrupt time
            ultraSONAR.timeNumber++;                            //Implement whether on up or down pulse
            if (ultraSONAR.timeNumber==2)                       //After up/down edges of feedback
            {
                ultraSONAR.distance = ultraSONAR.time[1]-ultraSONAR.time[0];    //Find length of pulse
                flag.ultraSONARRead = 1;                                        //Flag reading complete
                ultraSONAR.time[0] = 0;     //Reset up edge time
                ultraSONAR.time[1] = 0;     //Reset down edge time
                ultraSONAR.timeNumber=0;    //Reset to no pulse recieved
                TA0CCTL1 |= CM_1;   //Capture on rising edge
            }
            else
            {
                TA0CCTL1 |= CM_2;   //Capture on falling edge
            }
            TA0CCTL1 &= ~CCIFG;
            break;

        case TA0IV_TACCR2:  //TA0CCR2
            TA0CCTL2 &= ~CCIFG;
            break;

        case 0xA:   break;
    }
}

//Triggered by timer wrap
#pragma vector=TIMER1_A0_VECTOR
__interrupt void Timer1_A0_ISR (void)
{
    //If wrap occurs during reft ultrasonic pulse
    if (ultraLeft.timeNumber != 0)
    {
        ultraLeft.time[1] += TA1CCR0;
    }
	
    //If wrap occurs during right ultrasonic pulse
	if (ultraRight.timeNumber != 0)
    {
        ultraRight.time[1] += TA1CCR0;
    }
}
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
int main(void)
{
    //Stop watchdog timer
    WDTCTL = WDTPW | WDTHOLD;

    //Setup User Interface
    setupButton(&startButton);
    setupSwitch(&sideSelect);
    indicatorLEDSetup(&LEDRed);
    indicatorLEDSetup(&LEDBlue);
    indicatorLEDOff(&LEDRed);
    indicatorLEDOff(&LEDBlue);
	
	//DC Motor Setup
    motorSetup(&motorDrive);
    motorSetup(&motorSteer);
	
	//Ultrasonic Sensor Setup
    ultrasonicSetup(&ultraLeft);
	ultrasonicSetup(&ultraRight);
    ultrasonicSetup(&ultraSONAR);

    //Infrared Sensor Setup
    IRSetup(&IR);
	
	//Setup Servo Motor
	servoSetup(&servoSONAR);
	
	//Setup Internal Timers
	setupTimerSONAR();
    setupTimerSchedule();

    //Disable any initial unused Schedules
    Schedule.debounce.sec = 0;
    Schedule.debounce.ms = -1;

    Schedule.stateChange.sec = 0;
    Schedule.stateChange.ms = -1;

	Schedule.ultraLeftStart.sec = 0;
    Schedule.ultraLeftStart.ms = -1;
		
	Schedule.ultraRightStart.sec = 0;
    Schedule.ultraRightStart.ms = -1;

    Schedule.movementChange.sec = 0;
    Schedule.movementChange.ms = -1;

	Schedule.searchStart.sec = 0;
	Schedule.searchStart.ms = -1;


	//Start DC motor PWM schedules but set both motors output to do nothing
    timeIncrement(&Schedule.pwmMotorDrive, motorDrive.pwm.aSec, motorDrive.pwm.aMs);
    motorDrive.pwm.state = 1;
	motorDrive.direction = OFF;
    flag.motorDrive = 1;

    timeIncrement(&Schedule.pwmMotorSteer, motorSteer.pwm.aSec, motorSteer.pwm.aMs);
    motorSteer.pwm.state = 1;
	motorSteer.direction = STRAIGHT;
    flag.motorSteer = 1;

    //CANT REMEMBER WHAT THIS WAS FOR, TRY REMOVING XXX
    P1DIR |= BIT0;
    P1OUT &= ~(BIT0+BIT2);

	//Enable global interrupts
    __bis_SR_register(GIE);

	//Main loop
    while(1)
    {
        if (flag.timerA0)   //When timer ticks
        {
            checkSchedule();    //Check if time to do anything
            flag.timerA0 = 0;
        }
        else
        {
            checkFlags();       //Deal with events that occurred
			stateControl();		//Control car behaviour
        }
    }
}

//Function to set scheduled event. Input event to be scheduled and the time from now
//at which it should occur.
void timeIncrement(struct Time *time, int sec, int ms)
{
    //Always on next increment amount
    ms += TIMER_INC_MS;
    ms -= ms % TIMER_INC_MS;

    //Add to current time and if more then max ms add to seconds
    time->ms = currentTime.ms + ms;
    while(time->ms >= SECOND_COUNT)
    {
        time->ms -= SECOND_COUNT;
        sec++;
    }

    //Add to current time and if more then max wrap back to 0
    time->sec = currentTime.sec + sec;
    while(time->sec >= 300)
    {
        time->sec -= 300;
    }
}

//Check whether it is time for a particular event to occur
void checkSchedule()
{
    int incSec = 0;
    int incMs = 0;

	//Time for car to change behaviour
    if(isTime(Schedule.stateChange))
    {
		//Attend to in checkFlags()
        flag.stateChange = 1;
		
		//Disable schedule
        Schedule.stateChange.sec = 0;
        Schedule.stateChange.ms = -1;
    }
	
	//Time for car to start searching for can and not just driving forward
    if(isTime(Schedule.searchStart))
    {
		//Alters behaviour of search state()
        if (state == SEARCH)
        {
            search = 1;
        }
		
		//Disable schedule
        Schedule.searchStart.sec = 0;
        Schedule.searchStart.ms = -1;
    }

    //Time to trigger left ultrasonic
    if (isTime(Schedule.ultraLeftStart))
    {
        //Trigger ultrasonic
        ultrasonicTrigger(&ultraLeft);

        //Set a backup reading, code primarily works on doing something when a reading is returned
        //Therefore, if a reading is missed car will misbehave. Backup only triggers if reading not found
        //within 100 ms.
        timeIncrement(&Schedule.ultraLeftStartBackup, 0, 100);

        //Disable schedule
        Schedule.ultraLeftStart.sec = 0;
        Schedule.ultraLeftStart.ms = -1;
    }
	
    if (isTime(Schedule.ultraRightStart))
    {
        ultrasonicTrigger(&ultraRight);

        timeIncrement(&Schedule.ultraRightStartBackup, 0, 100);
	
        //Disable schedule
        Schedule.ultraRightStart.sec = 0;
        Schedule.ultraRightStart.ms = -1;
    }
	
	if (isTime(Schedule.ultraSONARStart))
    {
        ultrasonicTrigger(&ultraSONAR);

        timeIncrement(&Schedule.ultraSONARStartBackup, 0, 100);

        //Disable schedule
        Schedule.ultraSONARStart.sec = 0;
        Schedule.ultraSONARStart.ms = -1;
    }

    if (isTime(Schedule.ultraLeftStartBackup))
    {
        ultrasonicTrigger(&ultraLeft);

        //Disable schedule
        Schedule.ultraLeftStart.sec = 0;
        Schedule.ultraLeftStart.ms = -1;
    }

    if (isTime(Schedule.ultraRightStartBackup))
    {
        ultrasonicTrigger(&ultraRight);

        //Disable schedule
        Schedule.ultraRightStart.sec = 0;
        Schedule.ultraRightStart.ms = -1;
    }

    if (isTime(Schedule.ultraSONARStartBackup))
    {
        ultrasonicTrigger(&ultraSONAR);

        //Disable schedule
        Schedule.ultraSONARStart.sec = 0;
        Schedule.ultraSONARStart.ms = -1;
    }
	
    //Inter-state variable that allows the car to adopt a different behaviour after
    //so much time. For example, CIRCUMNAVIGATE does a number of movements to pass a
    //can and schedules when to change car headings when this scheduled event ocurs.
	if (isTime(Schedule.movementChange))
    {
        movement++;

        //Disable schedule
        Schedule.movementChange.sec = 0;
        Schedule.movementChange.ms = -1;
    }

	//Time to check button debouncing
    if(isTime(Schedule.debounce))
    {
		//Attend to in checkFlags()
        flag.debounce = 1;
		
		//Disable schedule
		Schedule.debounce.sec = 0;
        Schedule.debounce.ms = -1;
    }

	//Control PWM for DC motors
    if(isTime(Schedule.pwmMotorDrive))
    {
        if(motorDrive.pwm.state)	//If PWM high
        {
            //Find time to be LOW based on duration of HIGH and PWM period
            incSec = motorDrive.pwm.sec-motorDrive.pwm.aSec;
            incMs = motorDrive.pwm.ms-motorDrive.pwm.aMs;
			
			//Schedule time to become HIGH again
            timeIncrement(&(Schedule.pwmMotorDrive), incSec, incMs);
			
			//Set PWM low
            motorDrive.pwm.state = 0;
			
			//Attend to in checkFlags() to turn off motor as PWM is low
            flag.motorDrive = 1;
        }
        else						//If PWM low
        {
			//Set time to become LOW again
            timeIncrement(&Schedule.pwmMotorDrive, motorDrive.pwm.aSec, motorDrive.pwm.aMs);
            
			//Set PWM high
			motorDrive.pwm.state = 1;
			
			//Attend to in checkFlags() to turn on motor as PWM is high
            if (motorDrive.pwm.aMs == 0)
            {
				//If PWM is always low do not change as scheduler takes
				//short time to then make low again so motor is on momentarily
                flag.motorDrive = 0;
            }
            else
            {
                flag.motorDrive = 1;
            }
        }
    }

	//See behavioural comments above
    if(isTime(Schedule.pwmMotorSteer))
    {
        if(motorSteer.pwm.state)
        {
            incSec = motorSteer.pwm.sec-motorSteer.pwm.aSec;
            incMs = motorSteer.pwm.ms-motorSteer.pwm.aMs;
            timeIncrement(&(Schedule.pwmMotorSteer), incSec, incMs);
            motorSteer.pwm.state = 0;
            flag.motorSteer = 1;
        }
        else
        {
            timeIncrement(&Schedule.pwmMotorSteer, motorSteer.pwm.aSec, motorSteer.pwm.aMs);
            motorSteer.pwm.state = 1;
            if (motorSteer.pwm.aMs == 0)
            {
                flag.motorSteer = 0;
            }
            else
            {
                flag.motorSteer = 1;
            }
        }
    }

}
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

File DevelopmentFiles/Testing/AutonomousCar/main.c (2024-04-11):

/*
Filename    : AutonomousCar/main.c
Author      : Samuel Kliskey
Project     : EE579 Skittles Knocking Over Project
Date        : 20/1/24
Description : Main script to control functions of the autonomous vehicle
              to as quickly as possible knock over black skittles and avoid
              white skittles.

--------------------------------------------------------------------------------
Functions Present
--------------------------------------------------------------------------------
Port1_ISR()
Timer0_A0_ISR()

main(void);
checkFlags();
checkSchedule();
setupPins();
setupScheduleTimer();
timeIncrement();

--------------------------------------------------------------------------------
Change History
--------------------------------------------------------------------------------
20-JAN-2024 SARK created general structure
24-JAN-2024 SARK added DC motor / PWM functionality
06-FEB-2024 SARK added RI functionality for ultrasonic readings
11-FEB-2024 RI added distance 2 pulse length macro
21-FEB-2024 SARK corrections for steering alongside wall
--------------------------------------------------------------------------------
*/

//==============================================================================
// External Files
//------------------------------------------------------------------------------
#include <msp430.h>

//==============================================================================
// User-Defined Types
//------------------------------------------------------------------------------
//Define time variable
struct Time {
    int sec;
    int ms;
};

//Define Flags
struct flags {
	char button;
	char debounce;

	char stateChange;

	char timerA0;

	char motorA;
	char motorB;

	char ultraStart;
	char ultrasonicRead;

};

//Define Scheduler
struct Scheduler {
	struct Time debounce;

	struct Time stateChange;

	struct Time pwmMotorA;
	struct Time pwmMotorB;

	struct Time ultraStart;
};

//Define variable with PWM info
struct PWM {
	int sec;
	int ms;
    int aSec;
    int aMs;
	char state;
};

//Define variable which contains motor information
struct MotorDC {
    char direction; //Off (0), Forward (1) or Back(2)
    int pinA;
    int pinB;
    struct PWM pwm;
};

//Define variable containing servo motor information
struct Servo{
    int distance;
    int time[2];
    char timeNumber;
    char trigPin;
    char echoPin;
};

//Define variable containing ultrasonic sensor information
struct Ultrasonic{
    int distance;
	int time[2];
	char timeNumber;
	char trigPin;
    char echoPin;
};

//==============================================================================
// Function Prototypes
//------------------------------------------------------------------------------
__interrupt void Port1_ISR(void);
__interrupt void Timer0_A0_ISR(void);
__interrupt void Timer1_A1_ISR (void);

int     main(void);
void    checkFlags();
void    checkSchedule();
void    setupPins();
void    setupScheduleTimer();
void    timeIncrement(struct Time *time, int sec, int ms);
void	ultrasonicSetup(struct Ultrasonic ultra);
void    ultrasonicTrigger();
void    wallAlignment();
void 	motorOutput(struct MotorDC motor);
void 	motorSetup(struct MotorDC motor);

//==============================================================================
// MACRO
//------------------------------------------------------------------------------
#define SOUND_SPEED 343

#define SMCK_FREQ      1000000
#define ACLK_FREQ      32768

#define CLOCK_USED     SMCK_FREQ
#define LOW_POWER      LPM0
#define SECOND_COUNT   1000
#define TIMER_INC_MS   2

#define ULTRASONIC_CLOCK_USED ACLK_FREQ

#define isTime(X) ((currentTime.sec == X.sec) && (currentTime.ms == X.ms))
#define dist2pulse(d) ((ULTRASONIC_CLOCK_USED/100)*d*2/SOUND_SPEED)     // Converts a distance (cm) to ultrasonic sensor output pulse length

//States
#define START		0
#define GO			1
#define STOP		2

//Turn States
#define STRAIGHT    0
#define AWAY        1
#define CLOSE       2
#define STRAIGHTEN  3

#define WALLREADINGS  3

//RGB colours (P2OUT |= RGB_XX;)
#define RGB_RED     0x02
#define RGB_GREEN   0x08
#define RGB_BLUE    0x20
#define RGB_PURPLE  0x22
#define RGB_CYAN    0x28
#define RGB_YELLOW  0xA
#define RGB_WHITE   0x2A
//RGB off command: (P2OUT &= ~0x2A;)

//Motor direction commands
#define STRAIGHT    0
#define RIGHT       1
#define LEFT        2

#define OFF         0
#define FORWARD     1
#define BACK        2

//==============================================================================
// Global Variable Initialisation
//------------------------------------------------------------------------------
//Scheduling info
struct Time currentTime     =   {0, 0};    //Running count of time
struct Scheduler Schedule   =   {0};       //Schedule when events needing attended
struct flags flag           =   {0};       //Flag when something ready to be attended

//What car should be doing
char state	=	START;

//Motor info (On Port 1)
struct MotorDC motorA = {0, BIT4, BIT7, {0, 100, 0, 100, 1}};	//Drive
struct MotorDC motorB = {0, BIT5, BIT6, {0, 100, 0, 100, 1}};	//Direction

//Ultrasonic info (Port 2)
struct Ultrasonic ultraA = {0, {0, 0}, 0, BIT0, BIT2};
volatile int startingDistance;

//Distance to wall values
int wallTolerance = dist2pulse(5);
int canDetectDist = dist2pulse(20);

//Wall drive control
char turnState = STRAIGHT;
int  wallDistances[WALLREADINGS] = {0};
char turnStateTime = 0;



//==============================================================================
// Functions
//------------------------------------------------------------------------------

//Flag that button has been pressed and take out of LPM
#pragma vector=PORT1_VECTOR
__interrupt void Port1_ISR(void)
{
    flag.button = 1;
    __low_power_mode_off_on_exit();
    P1IFG &= ~BIT3;
    return;
}

//Flag that time has passed, update current time and take out of LPM
#pragma vector=TIMER0_A0_VECTOR
__interrupt void Timer0_A0_ISR(void)
{
    currentTime.ms += TIMER_INC_MS;
    if(currentTime.ms >= SECOND_COUNT)    //Increment timer
    {
        currentTime.ms -= SECOND_COUNT;
        if(++currentTime.sec == 60) currentTime.sec = 0;
    }

    flag.timerA0 = 1;

    __low_power_mode_off_on_exit();

    TA0CCTL0 &= ~CCIFG;
}
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

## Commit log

2024-01-20 Code Structure
    A basic code to turn on and off an LED with a button using a scheduler. Designed to be easy to build on throughout the project.
2024-01-24 Changes the PWM of two LEDS on Button Press
    Added structures for dc motors and PWM signals
2024-01-30 Basic Testing Platform Design
    [TestingPlatform_Assembly.0002.iam, TestingPlatform_Assembly.iam, TestingPlatform_base01.0006.ipt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]
2024-02-07 Not working ultrasonic
    Ross could you have a look at please
    [main.c]
2024-02-10 Ultrasonic Test
    Ross could you try running this on your microcontroller and see if it triggers the timer interrupt and measures the difference between times.
2024-02-11 Added Ultrasonic Testing Code
    [TestingPlatform_Assembly.0002.iam, TestingPlatform_Assembly.0003.iam, TestingPlatform_Assembly.iam]
2024-02-11 ultrasonic tested to work in main code
2024-02-13 Updated dist2pulse macro to insure it doesnt go out of range and changed steering motor control pins
2024-02-21 Wall Following Improvement
    Added functionality to slow / speed up the car if making large or small corrections. Also added functionality so that if it turns too far toward the wall and loses the distance to the wall then it will turn to straighten alongside wall
    [main.c]
2024-02-29 UltraServo Control Code
    Initial code to rotate servo whilst taking ultrasonic readings
2024-02-29 slight updates to code and CAD
    [TestingPlatform_base02.0012.ipt, TestingPlatform_base02.ipt, TestingPlatform_base02.stl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]
2024-04-01 Add files via upload
    IR code and IR housing. Will commit the updated code by tonight
    [Base.ipt, Head.ipt, IRSensorMount.iam]
2024-04-01 Improved Readability
    Can discuss at tomorrows meeting. Have now got three main loop functions. checkSchedule() checks scheduled event times. checkFlags() checks flags from schedules or other hardware sources and updates 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
2024-04-03 Ultrasonic Issues
    Updated SMCLK to be source always used. Trying to implement a design that uses two ultrasonics but the one on the RADAR does not work
    [Servo.c, main.c]
2024-04-04 Left Ultrasonic Definitley Wrking
2024-04-04 Should be called TimerInputChecks
2024-04-05 All the useful timer tests and car code that works with RADAR turning
2024-04-05 Mounting CAD created
    All CAD including: Ultrasonic Sensor mount, full base mount, IR top and bottom mount, servo mount (2 parts), ultrasonic sensor mount
    [BasePlate.0008.ipt, BasePlate.ipt, BasePlate.stl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]
2024-04-05 Initial PCB Creation
    [6140264816.iam, 6140266336.iam, 6140268416.iam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]
2024-04-05 Ultrasonic Testing Updated
2024-04-05 Parameterisable
    Changed macros so at start anything that will change, speed, wall tolerances ect. is defined at start and can be easily changed.
    [Servo.c, main.c]
2024-04-09 Initial Commit of AL's Infrared Sensor Functionality
2024-04-09 Infrared Functionality updated
    Renamed functions, removed debugging LEDs, allowed port selection and fixed small errors
2024-04-09 CAD versions
    [BasePlate.0008.ipt, BasePlate.0009.ipt, BasePlate.ipt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]
2024-04-09 Adding Right Ultrasonic and Merged Ross' Changes
2024-04-10 Improved Dealing with Ultrasonic Results
    Added averaging done by shift operations to be more computationally efficient. Also change should improve range achieved. Added code to disregard an ultrasonic value if it has only one erroneous valu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
2024-04-11 Final PCB Design
    [EE579_Skittles_PCB.PrjPcb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]
2024-04-13 Car Detects Colour and Realigns to Wall Using RADAR
    Wall realignment is not woring with RADAR. Going to try and reverse movements to get to can to get back to detection position
    [main.c]
2024-04-15 Wall Realignment with change in Wall Ultrasonic
    Bugs to fix but seems to work?
    [main.c]
2024-04-17 Initial Control Panel CAD & updated servo mounting CAD
    [ControlPanel01.0001.ipt, ControlPanel01.ipt, ControlPanel_Bottom.0010.ipt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]
2024-04-17 Updated Ultrasonic Mounts with bolt holes
    [Final_Assembly.0025.iam, Final_Assembly.0026.iam, Final_Assembly.iam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]
2024-04-19 Reorganised and final CAD
    [10_ControlPanel_Bottom.stl, 11_ControlPanel_Middle.stl, 12_ControlPanel_Top.stl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]
2024-04-22 Latest Update
    Including left and right wall alignment, improved wall alignment and other bug fixes.
    [DCMotor.c, main.c]
2024-04-22 Merging all folders of previous testing up to official hardware tests into a folder
    [Base.ipt, Head.ipt, IRSensorMount.iam]
2024-04-23 Initial BOM
    [BOM.xlsx]
2024-04-23 Updated BOM
    [BOM.xlsx]
2024-04-26 Small Changes
    Changed all reference from RADAR to SONAR. Slight (untested) improvement to wall realign.
2024-04-26 Tests into one project with single main control file to select tests
    (Has indicator LED, start button, drive and steer tests)
2024-04-26 Added servo test
2024-04-29 Final Version of Code
    Does not work perfectly, but all I had time to get to. Will find the first can and attempt to find the next but normally unsuccessful. Still needs optimisation in corridor for speeds and timings.
    [main.c]
2024-04-29 ultrasonic test
    Not yet tested or complted
2024-05-01 Version containing ultrasonic and IR sensor
    Only have slide switch to do now
2024-05-01 Most complete Version Yet
    Just need to test the side switch, maybe use readButton() and test everything on the car.
2024-05-02 All tests bar side select switch have been tested and verified on testbench
    Now need to test all 10 tests on the car
2024-05-02 Various Minor Bug Fixes
    [main.c]
2024-05-02 Added second LED, changed indicator LED, start button and slide tests
2024-05-02 LEDs, button, side confirmed working on car - everything else needs car tested
    drive, steer, servo, ultras, IR all work on testbench - SONAR P1.0 error
    [main.c]
2024-05-02 Updated hardware tests for ultrasonic working on final car
    1s initial delay was required to ensure stable power
2024-05-03 Changed structure of the repo to show development
    [Base.ipt, Head.ipt, IRSensorMount.iam]
2024-05-04 Adding updated Car approximation
    [6221480032.iam, 6221480992.iam, 6221482512.iam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]
2024-05-04 Assemblies, exploded diagrams and other components designed in CAD
    [Blue_LED.ipt, Bottom_Mount.0031.ipt, Bottom_Mount.0032.ipt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]
2024-05-04 Restructuring of CAD folder
    [4_UltrasonicSensorMount_backplate02.stl, 4_UltrasonicSensorMount_backplate03.stl, ControlPanel.0003.iam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]
2024-05-06 Updated Assemblies
    [MainAssembly_ServoStructure.0002.idw, MainAssembly_ServoStructure.0011.ipn, MainAssembly_ServoStructure.idw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]
2024-05-07 Finalised BOM
    [BOM.xlsx]
2024-05-08 BOM updated to correct errors & changed starting hardware test
    [BOM.xlsx]
